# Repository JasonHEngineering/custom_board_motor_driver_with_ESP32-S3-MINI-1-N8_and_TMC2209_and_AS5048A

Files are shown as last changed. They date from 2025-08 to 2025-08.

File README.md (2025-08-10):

# Custom board motor driver with_ESP32-S3-MINI-1-N8, TMC2209 and AS5048A
A custom board (42x42 mm - Nema 17) for driving bipolar stepper motors. Integrated with AS5048A - 14 bit absolute rotary encoder and TMC2209 silent stepper driver. Microstepping is programmable up to 64 micro-steps while max current draw capped by current sense R to be at 1.7A. 



gif_trial





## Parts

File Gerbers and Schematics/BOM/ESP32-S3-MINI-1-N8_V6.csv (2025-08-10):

Comment | Designator | Footprint | LCSC
FS55X226K500EHG | C1,C9 | Cap_MLCC_50V_22uF_X7R_2220_C784103:Cap_MLCC_50V_22uF_X7R_2220_C784103 | C784103
GRM155R71H223KA12D | C10 | MLCC_Murata_50V_22nF_X7R_±10%_0402_C77023:MLCC_Murata_50V_22nF_X7R_±10%_0402_C77023 | C77023
GRM188Z71C475KE21D | C11 | MLCC_Murata_16V_4pt7uF_X7R_±10%_0603_C389010:C0603 | C389010
GRM21BR61E106KA73L | C12 | 10uF_cap_GRM21BR61E106KA73L:CAPC2012X140N | C84416
CGA2B3X7R1V104KT0Y0F | C15,C16,C17 | TDK cap_100nF_35V_C0402_C343047:C0402_L1.0-W0.5-H0.5 | C343047
RVT1V101M0605 | C18 | Capacitor_100uF_35V_75mA@120Hz_±20%_D6pt3xL5pt4mm_C3151830:Capacitor_100uF_35V_75mA@120Hz_±20%_D6pt3xL5pt4mm_C3151830 | C3151830
CC0603KRX7R7BB105 | C2,C7 | MLCC_16V_1uF_X7R_±10%_0603_C106248:MLCC_16V_1uF_X7R_±10%_0603_C106248 | C106248
CC0603KRX7R9BB104 | C3,C8 | MLCC_Yageo_50V_100nF_X7R_±10%_0603_C14663:MLCC_Yageo_50V_100nF_X7R_±10%_0603_C14663 | C14663
GRM155R60J106ME15D | C4 | 10uF_cap_GRM155R60J106ME15D:CAPC1005X65N | C412251
GCM155R71C104KA55J | C5,C6,C13,C14,C19,C20 | 100nf_cap_GCM155R71C104KA55J:CAPC1005X55N | C2655418
BAT20JFILM | D2,D3 | diode_BAT20JFILM:SOD-323 | C155590
Conn_01x01_Female | J1,J2,J3,J4,J5 | Connector_PinHeader_1.00mm:PinHeader_1x01_P1.00mm_Vertical
SolderJumper_2_Open | JP1 | Jumper:SolderJumper-2_P1.3mm_Open_RoundedPad1.0x1.5mm
SolderJumper_3_Open | JP2,JP3,JP4 | Jumper:SolderJumper-3_P1.3mm_Open_RoundedPad1.0x1.5mm
FTC252012S100MBCA | L1 | Inductor_10uH_1pt6A_2x2pt5mm_C5832376:Inductor_10uH_1pt6A_2x2pt5mm_C5832376 | C5832376
RC0402FR-075K1L | R1,R13 | 5.1kR_RC0402FR-075K1L:RESC1005X40N | C105872
TC33X-2-103E | R11 | 10k_pot_TC33X-2-103E:TRIM_TC33X-2-103E | C719176
RL1206FR-7W0R11L | R2,R3 | Resistor_110mΩ_500mW_1206_C859923:Resistor_110mΩ_500mW_1206_C859923 | C859923
RC0402FR-0733RL | R4,R16,R17,R18 | Resistor_62.5mW_50V_±1%_33Ω_0402_C138002:Resistor_62.5mW_50V_±1%_33Ω_0402_C138002 | C138002
RC0402FR-0710KL | R5,R10,R12,R19,R22,R23,R24 | Resistor_62.5mW_50V_±1%_10kΩ_0402_C60490:Resistor_62.5mW_50V_±1%_10kΩ_0402_C60490 | C60490
RC0402FR-07100KL | R6,R7 | Resistor_ 100kΩ_62.5mW_50V_0402_C60491:Resistor_ 100kΩ_62.5mW_50V_0402_C60491 | C60491
FRC0805F1902TS | R8 | Resistor_19kΩ_0.125W_150V_0805_C2930177:Resistor_19kΩ_0.125W_150V_0805_C2930177 | C2930177
0402WGF4700TCE | R9,R14,R15 | Resistor_470Ω_62p5W_0402_C25117:Resistor_470Ω_62p5W_0402_C25117 | C25117
TS-1088-AR02016 | SW1,SW2 | 50mA_12V_1.6N__Tactile_Switches_C720477:50mA_12V_1.6N__Tactile_Switches_C720477 | C720477
TestPoint | TP1,TP2,TP3,TP4,TP5,TP6,TP7,TP8,TP9,TP10,TP11,TP12,TP13,TP14,TP15,TP16,TP17,TP18,TP19,TP20 | TestPoint:TestPoint_Pad_1.0x1.0mm
930-D-SMD-DS_02 | U1,U2 | WECO_1x2P_13.5A_Screw_Terminal_C19273347:WECO_1x2P_13.5A_Screw_Terminal_C19273347 | C19273347
ESP32-S3-MINI-1-N8 | U10 | ESP32-S3-MINI-1-N8_C2913206:BULETM-SMD_ESP32-S3-MINI-1-N8 | C2913206
S4B-XH-SM4-TB-(LF)(SN) | U11 | JST_4p_S4B-XH-SM4-TB(LF)(SN)_C161861:CONN-SMD_S4B-XH-SM4-TB-LF-SN | C161861
XL-1608UBC-06A | U12 | Blue_LED_5mA_456nm~476nm_130°_2.6V~3V_0603_C7371904:Blue_LED_5mA_456nm~476nm_130°_2.6V~3V_0603_C7371904 | C7371904
USBLC6-2SC6 | U3 | Package_TO_SOT_SMD:SOT-23-6 | C7519
TP6841S6-A | U4 | Step-down_800mA_4.5V_to_40V_SOT-23-6_C2844924:SOT-23-6_L2.9-W1.6-P0.95-LS2.8-BL | C2844924
TLV75733PDBVR | U5 | LDO_1A_Fixed_3.3V_out_5.5V_in_SOT-23-5_C485517:LDO_1A_Fixed_3.3V_out_5.5V_in_SOT-23-5_C485517 | C485517
AS5048A | U6 | Package_SO:TSSOP-14_4.4x5mm_P0.65mm | C2655181
20N06D | U7 | 60V_20A_28mΩ_2.5V_1-N-channel_PDFN-8(3x3)_MOSFETs_C7543835:60V_20A_28mΩ_2.5V_1-N-channel_PDFN-8(3x3)_MOSFETs_C7543835 | C7543835
NCV68061SNAIT1G | U8 | MOSFET_3V~32V_TSOP-6_Gate_Drivers_C5206748:TSOP-6_L3.0-W1.5-P0.95-BL | C5206748
TMC2209-LA-T | U9 | TRINAMIC_TMC2209-LA-T_C2150710:TRINAMIC_TMC2209-LA-T_C2150710 | C2150710
TYPE-C16PQTWT | USB1 | USB 3.1_C_3A_Surface_Mount_16P_C5187472:USB 3.1_C_3A_Surface_Mount_16P_C5187472 | C5187472

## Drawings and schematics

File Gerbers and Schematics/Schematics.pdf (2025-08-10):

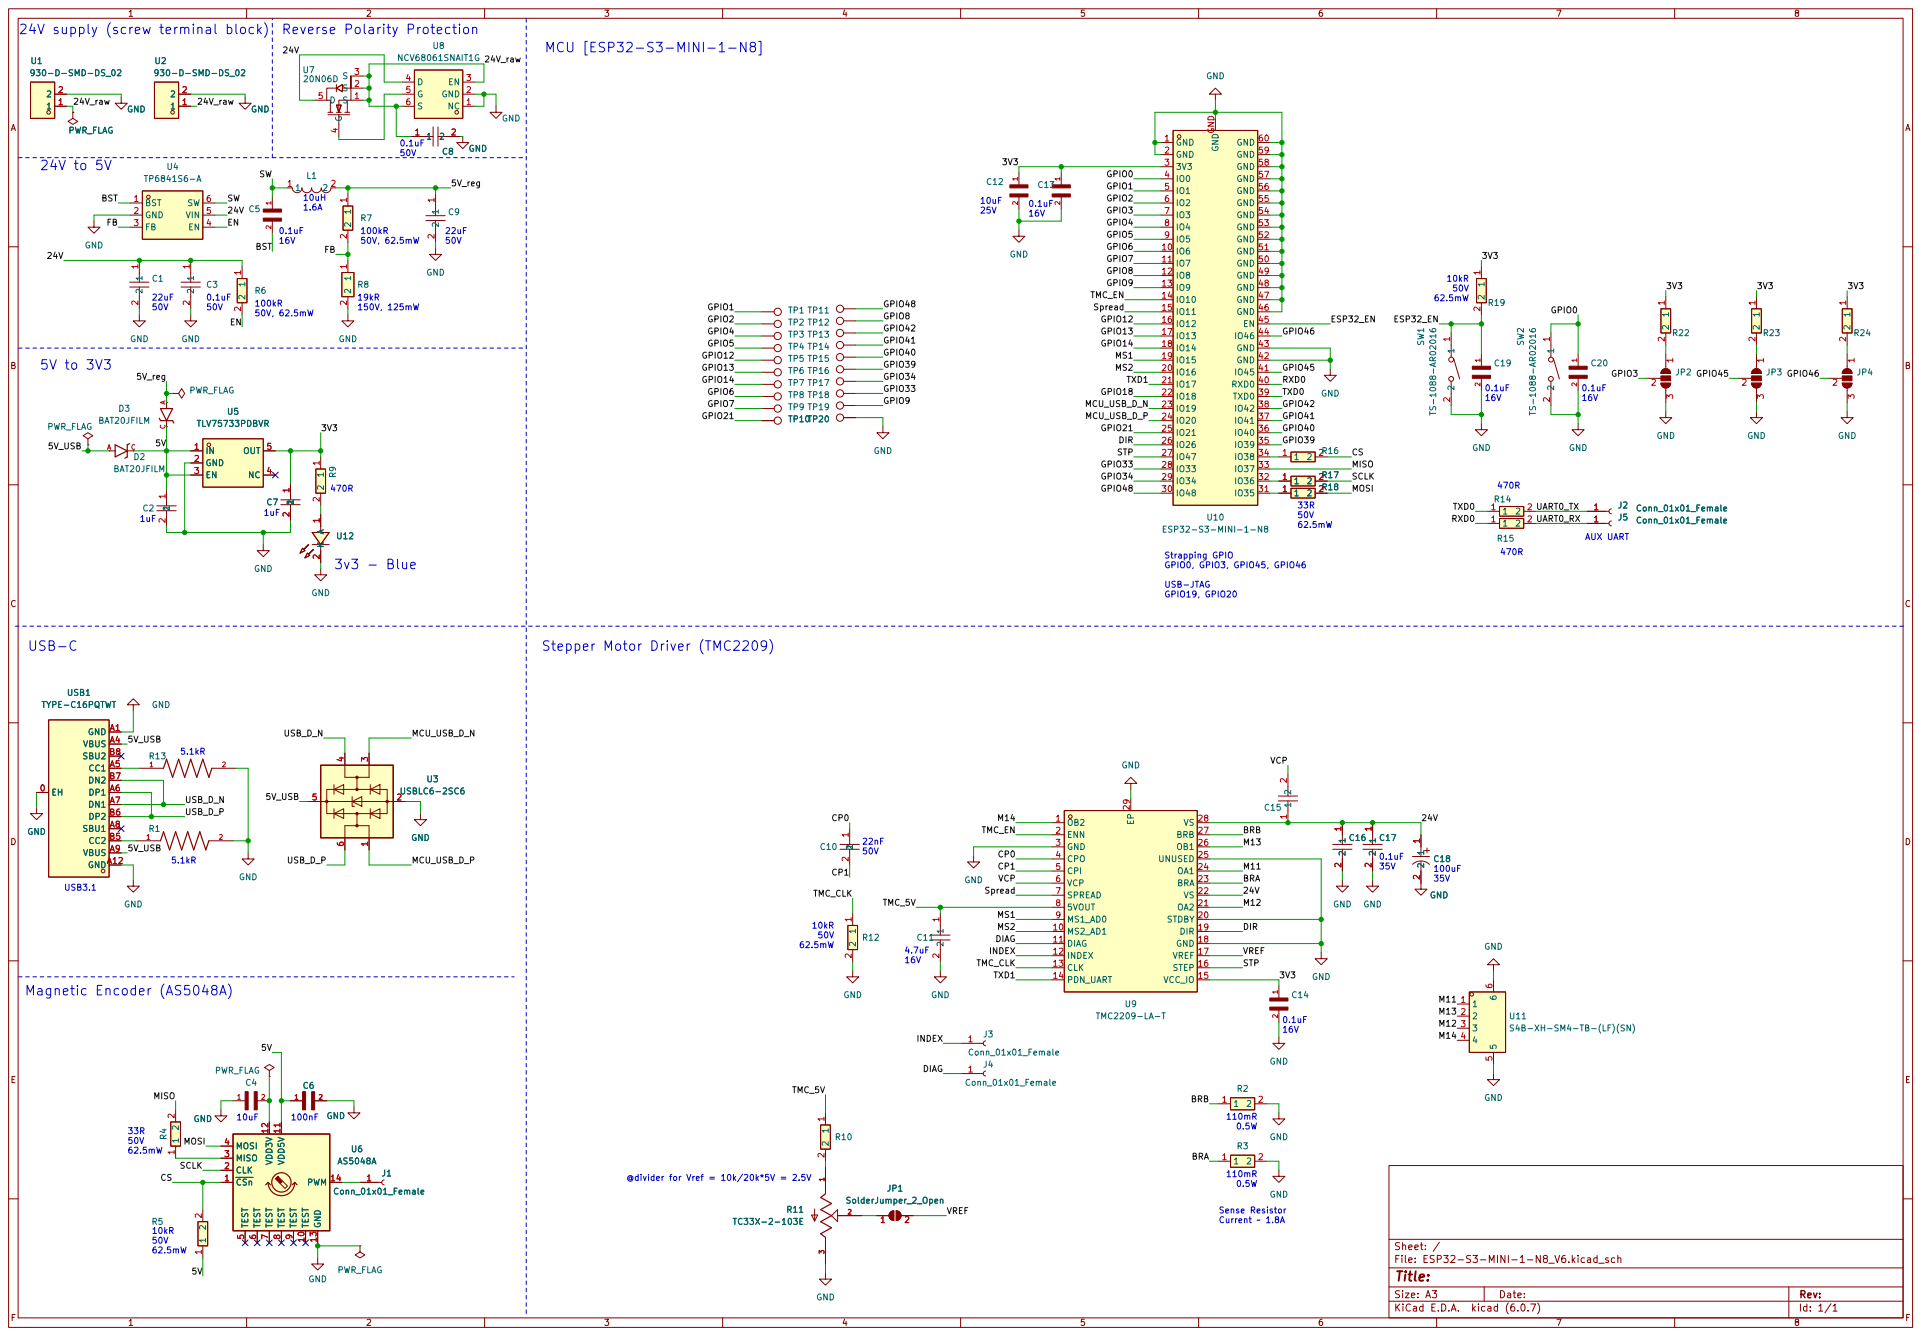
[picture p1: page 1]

1.6A 24V supply (screw terminal block)

1 2 C5 BST 1 GND 2 FB 3 EN 4 VIN 5 SW 6 U4 TP6841S6-A

AUX UART Strapping GPIO

6 U11S4B-XH-SM4-TB-(LF)(SN) GND GND

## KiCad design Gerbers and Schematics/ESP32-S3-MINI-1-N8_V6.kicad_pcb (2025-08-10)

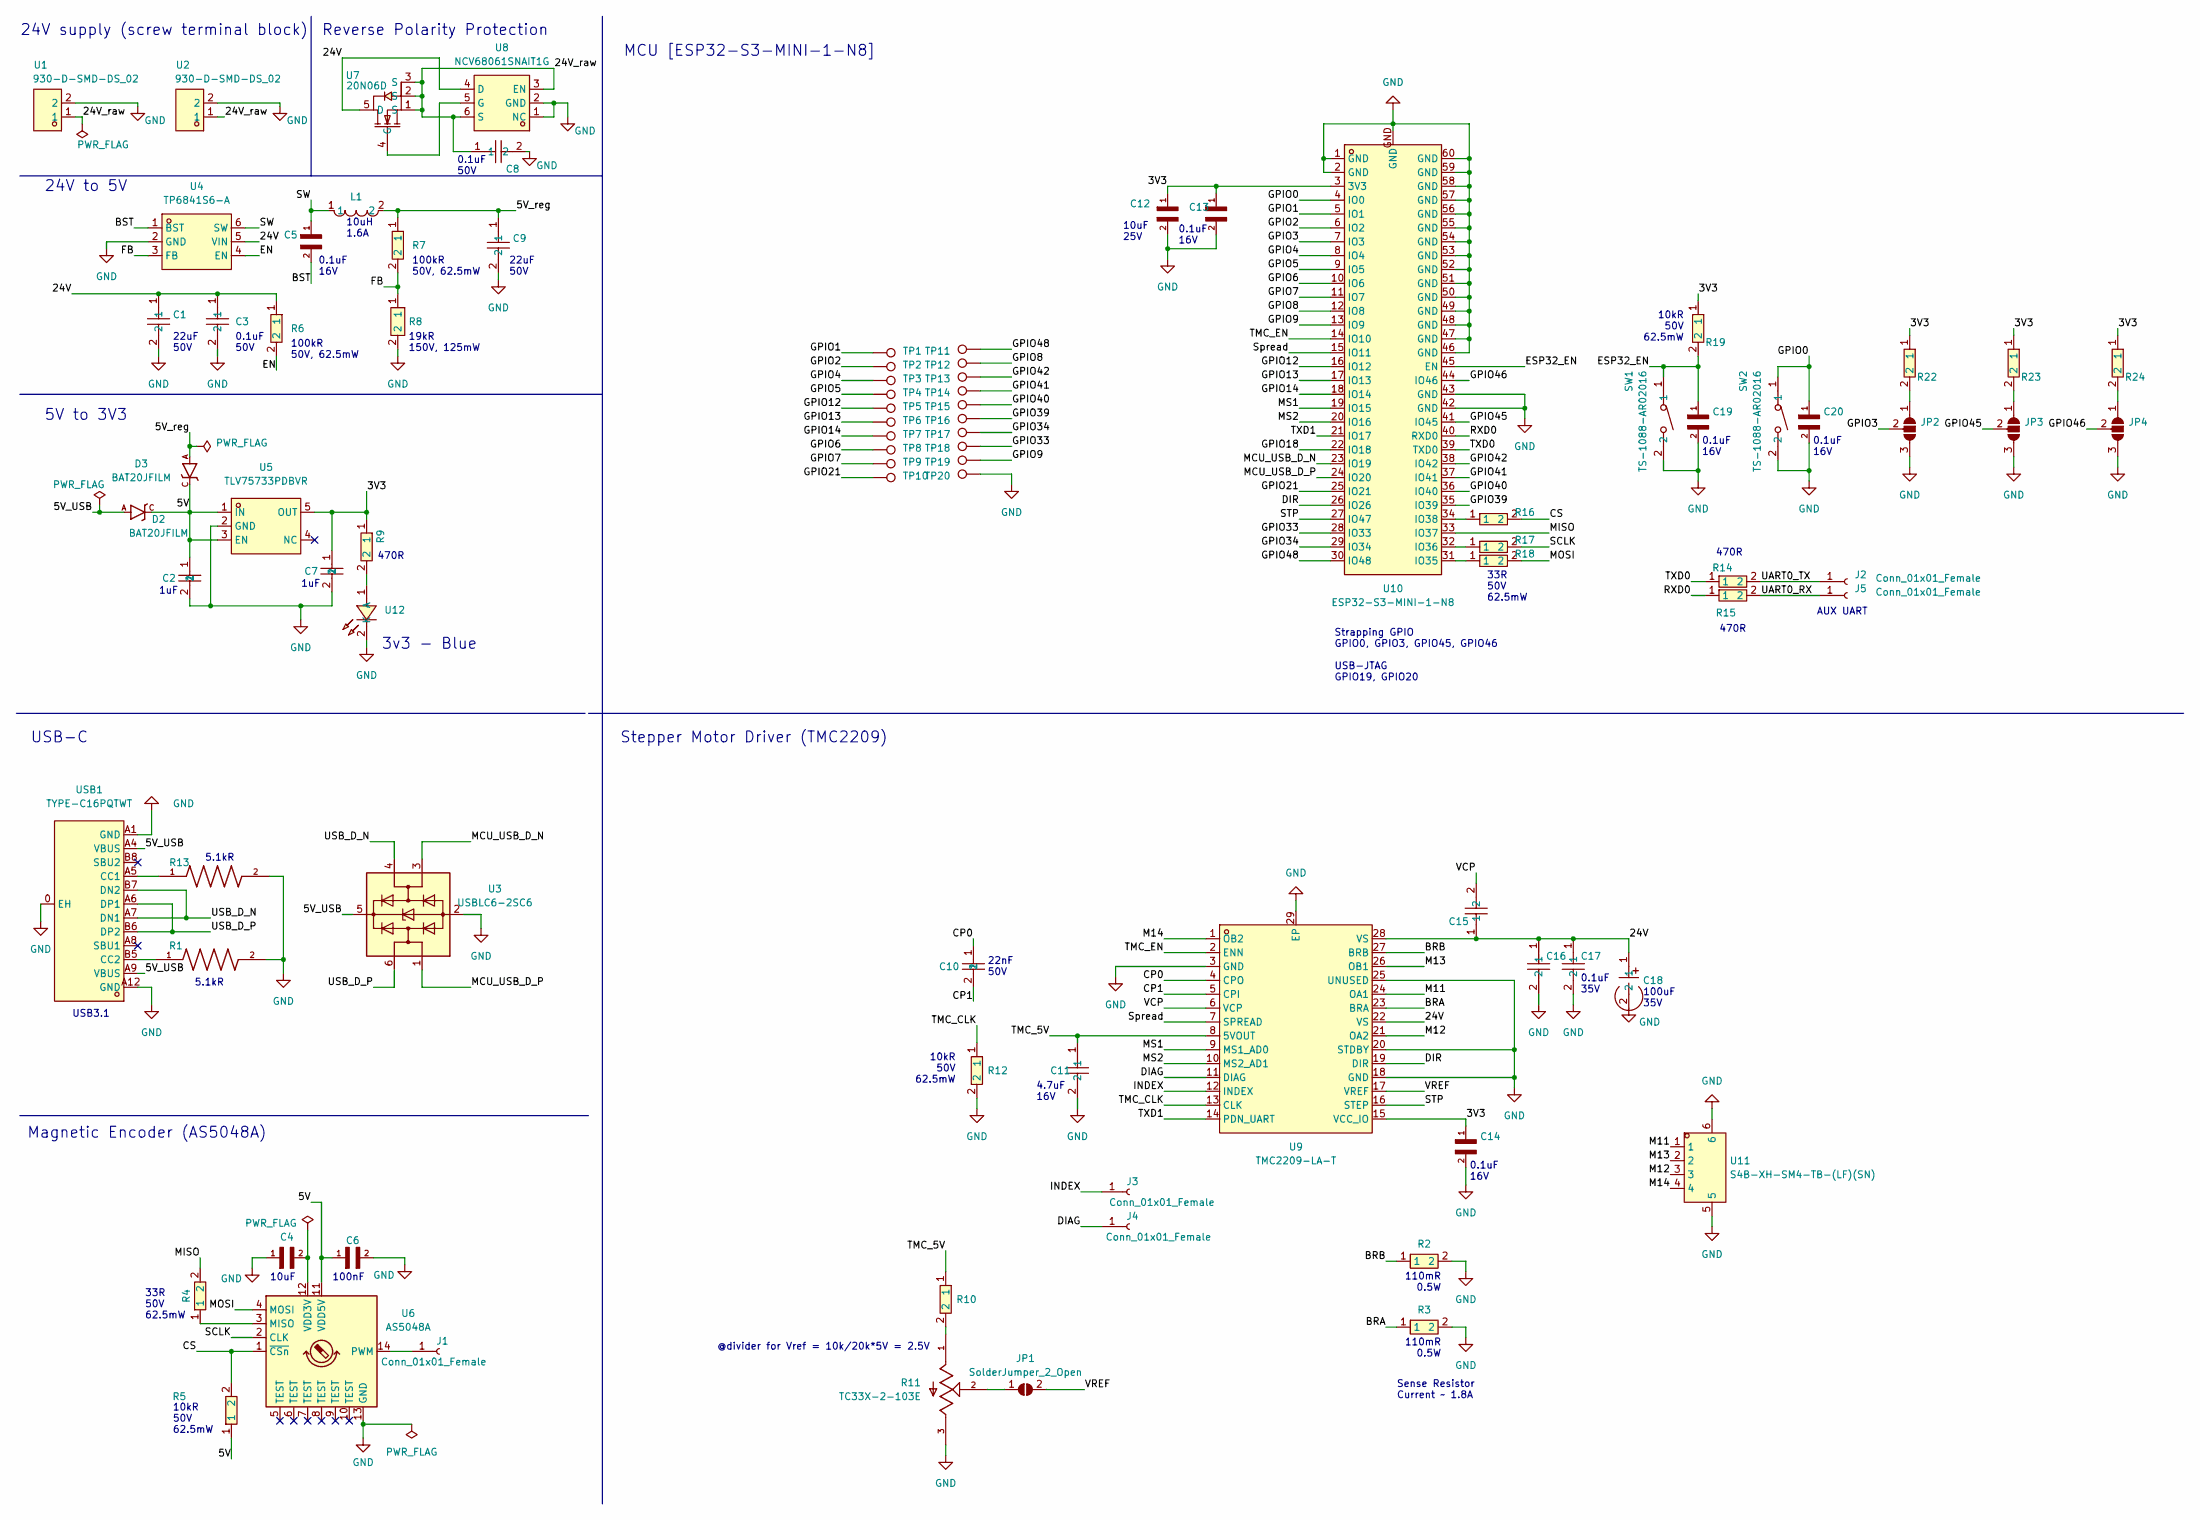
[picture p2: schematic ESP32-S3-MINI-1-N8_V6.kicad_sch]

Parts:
C1, C9: FS55X226K500EHG; Cap_MLCC_50V_22uF_X7R_2220_C784103; LCSC Part C784103
C2, C7: CC0603KRX7R7BB105; MLCC_16V_1uF_X7R_±10%_0603_C106248; LCSC Part C106248
C3, C8: CC0603KRX7R9BB104; MLCC_Yageo_50V_100nF_X7R_±10%_0603_C14663; LCSC Part C14663
C4: GRM155R60J106ME15D; CAPC1005X65N; LCSC C412251
C5, C13, C14, C19, C20: GCM155R71C104KA55J; CAPC1005X55N; LCSC Part # C2655418
C6: GCM155R71C104KA55J; CAPC1005X55N; LCSC C2655418
C10: GRM155R71H223KA12D; MLCC_Murata_50V_22nF_X7R_±10%_0402_C77023; LCSC Part C77023
C11: GRM188Z71C475KE21D; C0603; LCSC Part C389010
C12: GRM21BR61E106KA73L; CAPC2012X140N; LCSC Part # C84416
C15, C16, C17: CGA2B3X7R1V104KT0Y0F; C0402_L1.0-W0.5-H0.5; LCSC Part C343047
C18: RVT1V101M0605; Capacitor_100uF_35V_75mA@120Hz_±20%_D6pt3xL5pt4mm_C3151830; LCSC Part C3151830
D2, D3: BAT20JFILM; SOD-323; LCSC Part # C155590
J1, J2, J3, J4, J5: Conn_01x01_Female; PinHeader_1x01_P1.00mm_Vertical
JP1: SolderJumper_2_Open; SolderJumper-2_P1.3mm_Open_RoundedPad1.0x1.5mm
JP2, JP3, JP4: SolderJumper_3_Open; SolderJumper-3_P1.3mm_Open_RoundedPad1.0x1.5mm
L1: FTC252012S100MBCA; Inductor_10uH_1pt6A_2x2pt5mm_C5832376; LCSC Part C5832376
R1, R13: RC0402FR-075K1L; RESC1005X40N; LCSC Part # C105872
R2, R3: RL1206FR-7W0R11L; Resistor_110mΩ_500mW_1206_C859923; LCSC Part C859923
R4, R16, R17, R18: RC0402FR-0733RL; Resistor_62.5mW_50V_±1%_33Ω_0402_C138002; LCSC Part C138002
R5, R10, R12, R19, R22, R23, R24: RC0402FR-0710KL; Resistor_62.5mW_50V_±1%_10kΩ_0402_C60490; LCSC Part C60490
R6, R7: RC0402FR-07100KL; Resistor_ 100kΩ_62.5mW_50V_0402_C60491; LCSC Part C60491
R8: FRC0805F1902TS; Resistor_19kΩ_0.125W_150V_0805_C2930177; LCSC Part C2930177
R9, R14, R15: 0402WGF4700TCE; Resistor_470Ω_62p5W_0402_C25117; LCSC Part C25117
R11: TC33X-2-103E; TRIM_TC33X-2-103E; LCSC Part # C719176
SW1, SW2: TS-1088-AR02016; 50mA_12V_1.6N__Tactile_Switches_C720477; LCSC Part C720477
TP1, TP2, TP3, TP4, TP5, TP6, TP7, TP8, TP9, TP10, TP11, TP12, TP13, TP14, TP15, TP16, TP17, TP18, TP19, TP20: TestPoint; TestPoint_Pad_1.0x1.0mm
U1, U2: 930-D-SMD-DS_02; WECO_1x2P_13.5A_Screw_Terminal_C19273347; LCSC Part C19273347
U3: USBLC6-2SC6; SOT-23-6; LCSC Part # C7519
U4: TP6841S6-A; SOT-23-6_L2.9-W1.6-P0.95-LS2.8-BL; LCSC Part C2844924
U5: TLV75733PDBVR; LDO_1A_Fixed_3.3V_out_5.5V_in_SOT-23-5_C485517; LCSC Part C485517
U6: AS5048A; TSSOP-14_4.4x5mm_P0.65mm; LCSC C2655181
U7: 20N06D; 60V_20A_28mΩ_2.5V_1-N-channel_PDFN-8(3x3)_MOSFETs_C7543835; LCSC Part C7543835
U8: NCV68061SNAIT1G; TSOP-6_L3.0-W1.5-P0.95-BL; LCSC Part C5206748
U9: TMC2209-LA-T; TRINAMIC_TMC2209-LA-T_C2150710; LCSC Part C2150710
U10: ESP32-S3-MINI-1-N8; BULETM-SMD_ESP32-S3-MINI-1-N8; LCSC Part C2913206
U11: S4B-XH-SM4-TB-(LF)(SN); CONN-SMD_S4B-XH-SM4-TB-LF-SN; LCSC Part C161861
U12: XL-1608UBC-06A; Blue_LED_5mA_456nm~476nm_130°_2.6V~3V_0603_C7371904; LCSC Part C7371904
USB1: TYPE-C16PQTWT; USB 3.1_C_3A_Surface_Mount_16P_C5187472; LCSC Part C5187472

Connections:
/3V3: C7.1, C12.1, C13.1, C14.1, R9.1, R19.1, R22.1, R23.1, R24.1, U5.5 (OUT), U9.15 (VCC_IO), U10.3 (3V3)
/5V: C2.1, C6.1, D2.C, D3.C, R5.1, U5.1 (IN), U5.3 (EN), U6.11 (VDD5V)
/5V_USB: D2.A, U3.5 (VBUS), USB1.A4 (VBUS), USB1.A9 (VBUS)
/5V_reg: C9.1, D3.A, L1.2, R7.1
/24V: C1.1, C3.1, C15.1, C16.1, C17.1, C18.1, R6.1, U4.5 (VIN), U7.5 (D), U8.4 (D), U9.22 (VS), U9.28 (VS)
/24V_raw: C8.1, U1.1, U2.1, U7.1 (S), U7.2 (S), U7.3 (S), U8.3 (EN), U8.6 (S)
/BRA: R3.1, U9.23 (BRA)
/BRB: R2.1, U9.27 (BRB)
/BST: C5.2, U4.1 (BST)
/CP0: C10.1, U9.4 (CPO)
/CP1: C10.2, U9.5 (CPI)
/CS: R5.2, R16.2, U6.1 (~CSn)
/DIAG: J4.1, U9.11 (DIAG)
/DIR: U9.19 (DIR), U10.26 (IO26)
/EN: R6.2, U4.4 (EN)
/ESP32_EN: C19.1, R19.2, SW1.1, U10.45 (EN)
/FB: R7.2, R8.1, U4.3 (FB)
/GPIO0: C20.1, SW2.1, U10.4 (IO0)
/GPIO1: TP1.1, U10.5 (IO1)
/GPIO2: TP2.1, U10.6 (IO2)
/GPIO3: JP2.2 (C), U10.7 (IO3)
/GPIO4: TP3.1, U10.8 (IO4)
/GPIO5: TP4.1, U10.9 (IO5)
/GPIO6: TP8.1, U10.10 (IO6)
/GPIO7: TP9.1, U10.11 (IO7)
/GPIO8: TP12.1, U10.12 (IO8)
/GPIO9: TP19.1, U10.13 (IO9)
/GPIO12: TP5.1, U10.16 (IO12)
/GPIO13: TP6.1, U10.17 (IO13)
/GPIO14: TP7.1, U10.18 (IO14)
/GPIO18: U10.22 (IO18)
/GPIO21: TP10.1, U10.25 (IO21)
/GPIO33: TP18.1, U10.28 (IO33)
/GPIO34: TP17.1, U10.29 (IO34)
/GPIO39: TP16.1, U10.35 (IO39)
/GPIO40: TP15.1, U10.36 (IO40)
/GPIO41: TP14.1, U10.37 (IO41)
/GPIO42: TP13.1, U10.38 (IO42)
/GPIO45: JP3.2 (C), U10.41 (IO45)
/GPIO46: JP4.2 (C), U10.44 (IO46)
/GPIO48: TP11.1, U10.30 (IO48)
/INDEX: J3.1, U9.12 (INDEX)
/M11: U9.24 (OA1), U11.1
/M12: U9.21 (OA2), U11.3
/M13: U9.26 (OB1), U11.2
/M14: U9.1 (OB2), U11.4
/MCU_USB_D_N: U3.3 (I/O2), U10.23 (IO19)
/MCU_USB_D_P: U3.1 (I/O1), U10.24 (IO20)
/MISO: R4.2, U10.33 (IO37)
/MOSI: R18.2, U6.4 (MOSI)
/MS1: U9.9 (MS1_AD0), U10.19 (IO15)
/MS2: U9.10 (MS2_AD1), U10.20 (IO16)
/RXD0: R15.1, U10.40 (RXD0)
/SCLK: R17.2, U6.2 (CLK)
/STP: U9.16 (STEP), U10.27 (IO47)
/SW: C5.1, L1.1, U4.6 (SW)
/Spread: U9.7 (SPREAD), U10.15 (IO11)
/TMC_5V: C11.1, R10.1, U9.8 (5VOUT)
/TMC_CLK: R12.1, U9.13 (CLK)
/TMC_EN: U9.2 (ENN), U10.14 (IO10)
/TXD0: R14.1, U10.39 (TXD0)
/TXD1: U9.14 (PDN_UART), U10.21 (IO17)
/UART0_RX: J5.1, R15.2
/UART0_TX: J2.1, R14.2
/USB_D_N: U3.4 (I/O2), USB1.A7 (DN1), USB1.B7 (DN2)
/USB_D_P: U3.6 (I/O1), USB1.A6 (DP1), USB1.B6 (DP2)
/VCP: C15.2, U9.6 (VCP)
/VREF: JP1.2 (B), U9.17 (VREF)
GND: C1.2, C2.2, C3.2, C4.1, C6.2, C7.2, C8.2, C9.2, C11.2, C12.2, C13.2, C14.2, C16.2, C17.2, C18.2, C19.2, C20.2, JP2.3 (B), JP3.3 (B), JP4.3 (B), R1.2, R2.2, R3.2, R8.2, R11.3, R12.2, R13.2, SW1.2, SW2.2, TP20.1, U1.2, U2.2, U3.2 (GND), U4.2 (GND), U5.2 (GND), U6.13 (GND), U8.1 (NC), U8.2 (GND), U9.3 (GND), U9.18 (GND), U9.20 (STDBY), U9.25 (UNUSED), U9.29 (EP), U10.1 (GND), U10.2 (GND), U10.42 (GND), U10.43 (GND), U10.46 (GND), U10.47 (GND), U10.48 (GND), U10.49 (GND), U10.50 (GND), U10.51 (GND), U10.52 (GND), U10.53 (GND), U10.54 (GND), U10.55 (GND), U10.56 (GND), U10.57 (GND), U10.58 (GND), U10.59 (GND), U10.60 (GND), U10.GND, U11.5, U11.6, U12.2 (K), USB1.0 (EH), USB1.A1 (GND), USB1.A12 (GND)
unnamed: C4.2, U6.12 (VDD3V)
unnamed: J1.1, U6.14 (PWM)
unnamed: JP1.1 (A), R11.2
unnamed: JP2.1 (A), R22.2
unnamed: JP3.1 (A), R23.2
unnamed: JP4.1 (A), R24.2
unnamed: R1.1, USB1.B5 (CC2)
unnamed: R4.1, U6.3 (MISO)
unnamed: R9.2, U12.1 (A)
unnamed: R10.2, R11.1
unnamed: R13.1, USB1.A5 (CC1)
unnamed: R16.1, U10.34 (IO38)
unnamed: R17.1, U10.32 (IO36)
unnamed: R18.1, U10.31 (IO35)
unnamed: U7.4 (G), U8.5 (G)

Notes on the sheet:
10uF
0.1uF 16V
22uF 50V
100kR 50V, 62.5mW
470R
5.1kR
Reverse Polarity Protection
Sense Resistor Current ~ 1.8A
110mR 0.5W
@divider for Vref = 10k/20k*5V = 2.5V
1uF
33R 50V 62.5mW
10kR 50V 62.5mW
USB3.1
5V to 3V3
USB-C
0.1uF 50V
0.1uF 35V
Strapping GPIO GPIO0, GPIO3, GPIO45, GPIO46 USB-JTAG GPIO19, GPIO20
19kR 150V, 125mW
24V supply (screw terminal block)
MCU [ESP32-S3-MINI-1-N8]
AUX UART
10uH 1.6A
Magnetic Encoder (AS5048A)
100uF 35V
24V to 5V
4.7uF 16V
10uF 25V
Stepper Motor Driver (TMC2209)
3v3 - Blue
100nF
22nF 50V

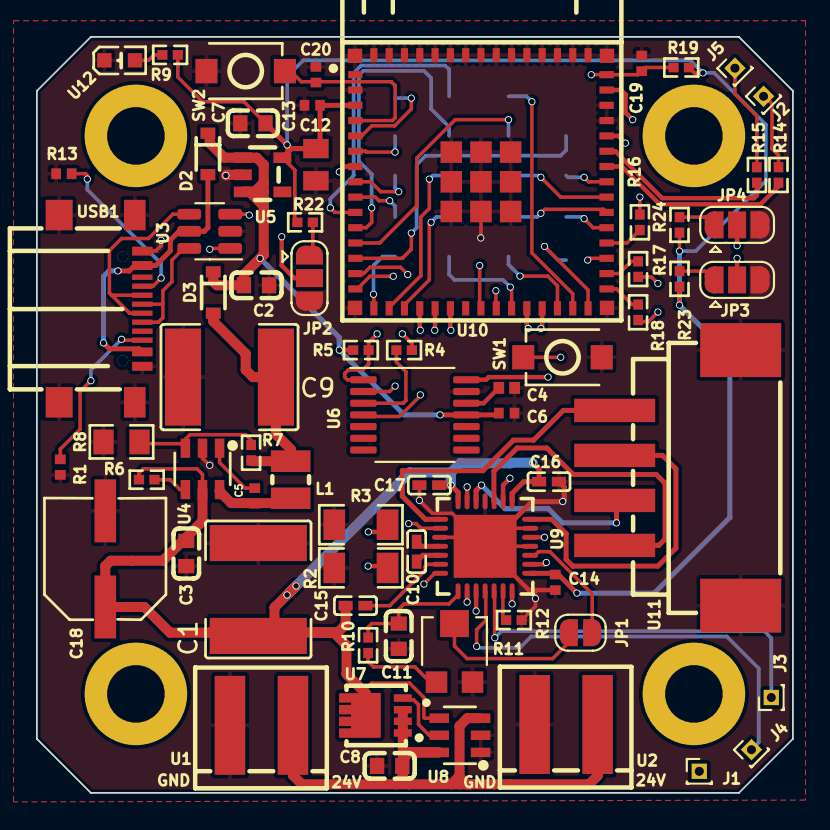
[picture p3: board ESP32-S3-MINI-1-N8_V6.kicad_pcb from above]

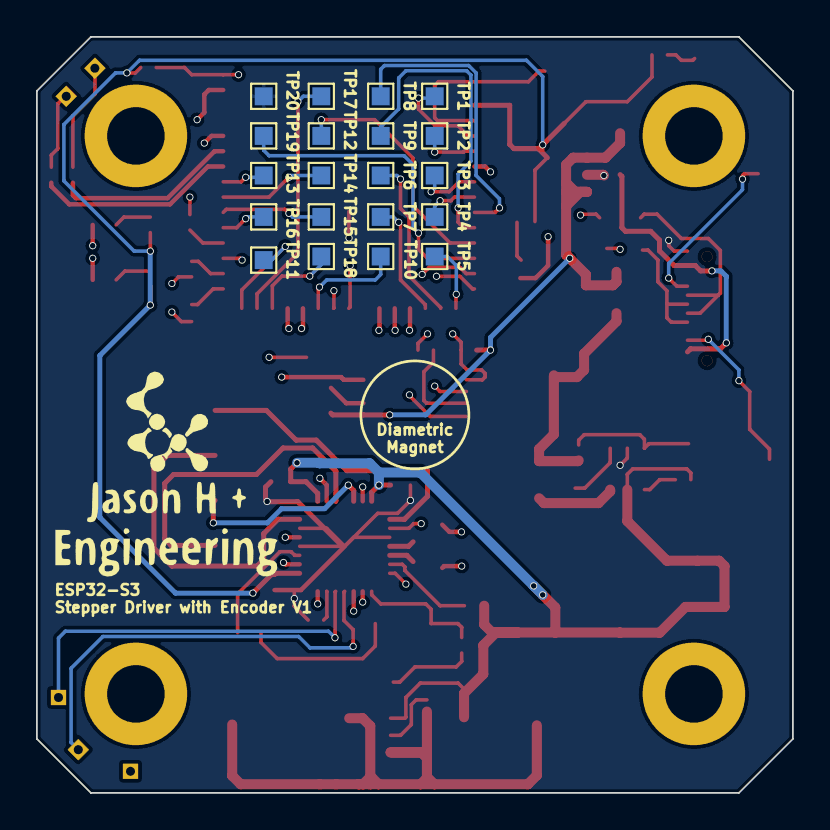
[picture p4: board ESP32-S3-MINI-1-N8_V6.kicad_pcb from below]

Board: 4 copper layers, 42.0 x 42.0 mm, 89 parts (20 on the bottom side), 83 nets.

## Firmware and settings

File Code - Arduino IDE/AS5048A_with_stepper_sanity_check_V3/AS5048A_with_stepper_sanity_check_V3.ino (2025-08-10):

// V1 pure reading of AS5048A only
// V2 with stepper
// V3 with PID - slow 

#include <AccelStepper.h>
#include <SPI.h>

/*PINS
   Arduino SPI pins
   MOSI = 11, MISO = 12, SCK = 13, CS = 10

   STM32 SPI pins
   MOSI = PA7, MISO = PA6, SCK = PA5, CS = PA4

   ESP32_S3_DevKit_C1_N16R8 SPI pins
   MOSI = 11, MISO = 12, SCK = 13, CS = per assignment as needed

   ESP32-S3-MINI-1-N8 custom board SPI pins
   MOSI = 11, MISO = 12, SCK = 13, CS = per assignment as needed
*/

// SPI lines for my custom ESP32-S3-MINI-1-N8
#define SPI_CS 38
#define SPI_MISO 37
#define SPI_SCLK 36
#define SPI_MOSI 35


// For my custom ESP32-S3-MINI-1-N8 with TMC2209
#define stepper_1_stepPin 47
#define stepper_1_dirPin 26
#define stepper_1_MS1 15
#define stepper_1_MS2 16

// Define motor interface type
#define motorInterfaceType 1 //AccelStepper::DRIVER (1) means a stepper driver (with Step and Direction pins)
#define no_of_steppers 1

// #define movesteps 256000

//define an array of stepper pointers. initialize the pointer to NULL (null pointer) for safety (see below)
AccelStepper *steppers[no_of_steppers] = {NULL};

float axis_degAngle[no_of_steppers] = {0}; //Angle in degrees
float accepted_axis_degAngle[no_of_steppers] = {0}; //Angle in degrees
const int windowSize = 1; // Adjust the window size based on your requirements
int currentIndex = 0;
uint16_t rawData = 0; //bits from the encoder (16 bits, but top 2 has to be discarded)
uint16_t command = 0b1111111111111111; //read command (0xFFF)
float sensorValues[no_of_steppers][windowSize];
const float start_axis_degAngle[no_of_steppers] = {177.74}; //Angle in degrees, encoder values when in kinematic zeroed position - 19-Apr-25

#define STEPS_PER_REV 6400   // Steps per full revolution (adjust to your setup) 32*200=6400

// float struct to store angles 
struct {
   float angles_array[no_of_steppers]; // unit: °
} encoder; 



// PID loop constants (tune for your system)
float Kp = 1508.0;
float Kd = 0.02;
float lastError = 0;
unsigned long lastTime = 0;

// Target angle in degrees (0 to 360)
float targetAngle = 160.0;



void setup() {

  SPI.begin(SPI_SCLK, SPI_MISO, SPI_MOSI); //SCLK, MISO, MOSI, SS
  pinMode(SPI_CS, OUTPUT); // set all CS pin as output
  digitalWrite(SPI_CS, HIGH);
  Serial.begin(9600); // start serial for output
  delay(100);


  // Create stepper instances
  steppers[0] = new AccelStepper(motorInterfaceType, stepper_1_stepPin, stepper_1_dirPin);

  // Configure micro-stepping
  // MS1 - LOW, MS2 - LOW ==> 1/8
  // MS1 - LOW, MS2 - HIGH ==> 1/64
  // MS1 - HIGH, MS2 - LOW ==> 1/32
  // MS1 - HIGH, MS2 - HIGH ==> 1/16

 if (steppers[0]) {
    pinMode(stepper_1_MS1, OUTPUT);
    digitalWrite(stepper_1_MS1, HIGH);
    pinMode(stepper_1_MS2, OUTPUT);
    digitalWrite(stepper_1_MS2, LOW);
 }

  // Configure each stepper as needed
 if (steppers[0]) {
    steppers[0]->setMaxSpeed(32000); //steps per second, not more than 32000 for TMC2209 
    steppers[0]->setAcceleration(8000.0); //desired acceleration in steps per second per second, not more than 8000 for TMC2209 
    //steppers[0]->moveTo(movesteps);   
 }

}

void loop() {
  // put your main code here, to run repeatedly:
  read_angle_Register(); //read the position of the magnet
  //report_angle();

	// Move the motor one step
	// steppers[0]->run();


  // Time delta
  unsigned long now = millis();
  float dt = (now - lastTime) / 1000.0;
  lastTime = now;

  // Read encoder angle
  float currentAngle = getMovingAverage(0); //read the position of the magnet
  if (currentAngle < 0) currentAngle += 360;  // Normalize

  // Error (shortest direction)
  float error = targetAngle - currentAngle;
  if (error > 180) error -= 360;
  if (error < -180) error += 360;

  // Derivative
  float derivative = (error - lastError) / dt;
  lastError = error;

  // PID control output (no integral used here)
  float output = Kp * error + Kd * derivative;

  // Convert angle error to stepper steps
  float stepsToMove = (output / 360.0) * STEPS_PER_REV;

  // Move stepper (relative move)
  steppers[0]->setSpeed(stepsToMove);
  steppers[0]->runSpeed();

  // Debug
  Serial.print("Target: "); Serial.print(targetAngle);
  Serial.print(" | Current: "); Serial.print(currentAngle);
  Serial.print(" | Error: "); Serial.print(error);
  Serial.print(" | Output: "); Serial.println(output);
  
  //delay(1);
  delayMicroseconds(50);  // Delay for 50 micro seconds

}

void read_angle_Register()
{
  for (int i = 0; i <= (no_of_steppers-1); i++) {
    
    SPI.beginTransaction(SPISettings(4000000, MSBFIRST, SPI_MODE1));
    //SPI.setClockDivider(SPI_CLOCK_DIV64);
      
    //--sending the command
    digitalWrite(SPI_CS, LOW);
    SPI.transfer16(command);
    digitalWrite(SPI_CS, HIGH);
  
    //--receiving the reading
    digitalWrite(SPI_CS, LOW);
    rawData = SPI.transfer16(command);
    digitalWrite(SPI_CS, HIGH);
    
    SPI.endTransaction();
  
    rawData = rawData & 0b0011111111111111; //removing the top 2 bits (PAR and EF)
  
    axis_degAngle[i] = (float)rawData / 16383.0 * 360.0; //16384 = 2^14, 360 = 360 degrees, however for real resolution, take 2^14 - 1 = 16383
    updateMovingAverage(i, axis_degAngle[i]);

    // Note: if getMovingAverage(i) == 360.00, it is likely to be false/no reading
    if ((axis_degAngle[i] != 0.00) && (getMovingAverage(i) != 0.00)){
      accepted_axis_degAngle[i] = getMovingAverage(i);
      encoder.angles_array[i] = fmod(((accepted_axis_degAngle[i]-start_axis_degAngle[i])+180.0),360.0)-180.0;

    }
  }
}

void updateMovingAverage(int axis, float newValue) {
  // Update the array with the new value
  sensorValues[axis][currentIndex] = newValue;

  // Move to the next index in a circular manner
  if (axis==(no_of_steppers-1)){
    currentIndex = (currentIndex + 1) % windowSize;
  }
}


float getMovingAverage(int axis) {
  // Calculate the average of the values in the array
  float sum = 0;
  for (int i = 0; i < windowSize; i++) {
    sum += sensorValues[axis][i];
  }
  float local_window = windowSize;
  float moving_average = sum / local_window;
  return moving_average;
}



void report_angle()
{
  for(int j = 0; j <= (no_of_steppers-1); j++) {
      //Serial.println(String(j+1) + " " + getMovingAverage(j));
      Serial.println(String("Angle: ") + getMovingAverage(j));
      //Serial.println(String(j+1) + " " + encoder.angles_array[j]);
    }
    Serial.flush();
}
